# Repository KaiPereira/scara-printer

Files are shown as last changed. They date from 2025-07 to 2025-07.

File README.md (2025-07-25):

# Double Arm Scara 2D Printer

This scara printer uses a double arm scara 5-bar linkage system to be able to print in XY and utilize the floor as a bed to create a cost-effective, efficient printer/pen plotter. This printer was built for undercity, a 4 day hackathon by @lordbagel42, @vibsthebot and @KaiPereira. [Slightly Working Demo](https://www.youtube.com/shorts/rTIAOmObG48)

Pasted image 20250714064541.png

## Custom Features

- Double scara arm giving X and Y movement
- 2 wheel drivetrain which gives movement on the Z, and allows it to print in an infinitely large area
- 3D pen for the extruder/hotend giving an economical and cool way to print
- Support for Seeed XIAO RP2040 and Nema 17 motors
- Cost effective and simple design

## Cad Design

The entire design was built in Onshape by all three of us, the drivetrain is the fundamental part and uses weight to hold up the scara and 3D pen, the 3D pen is then held in using a mount and we use bearings and nema 17's for everything else. The entire project was also 3D printed aside from the electronics, screws, bearings, etc.

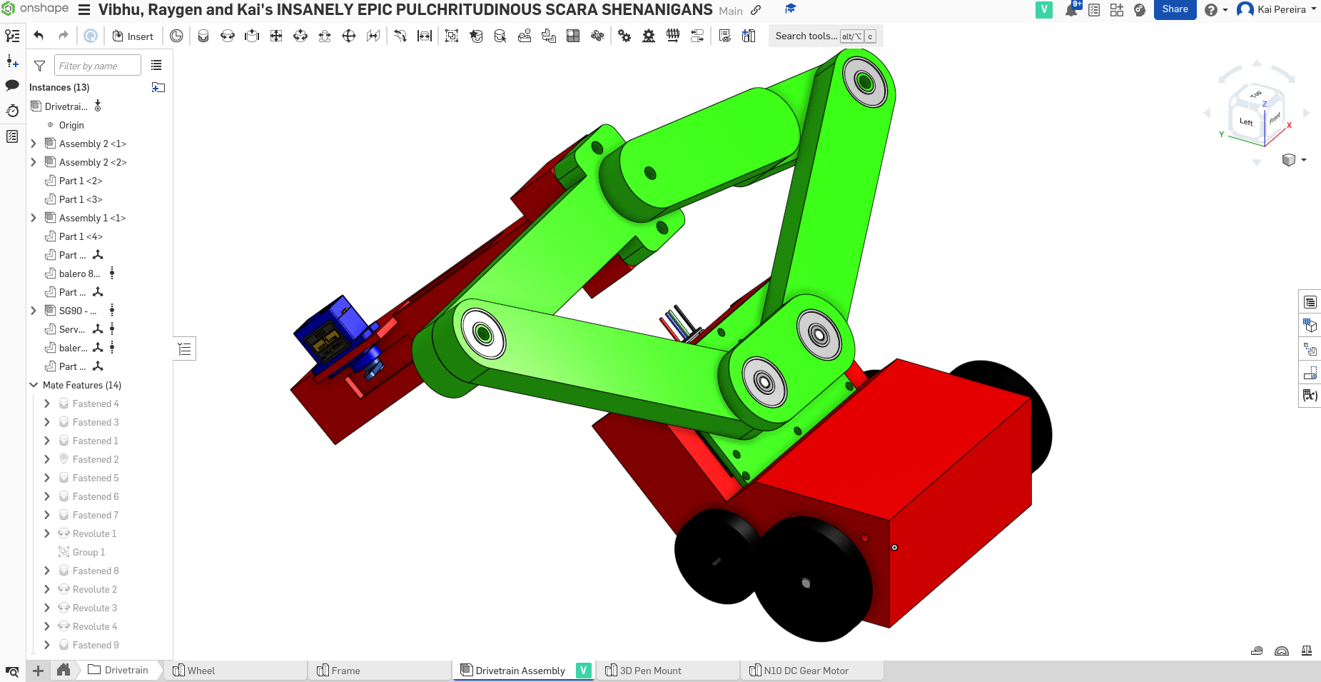
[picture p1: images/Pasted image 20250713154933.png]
Pasted image 20250713154933.png

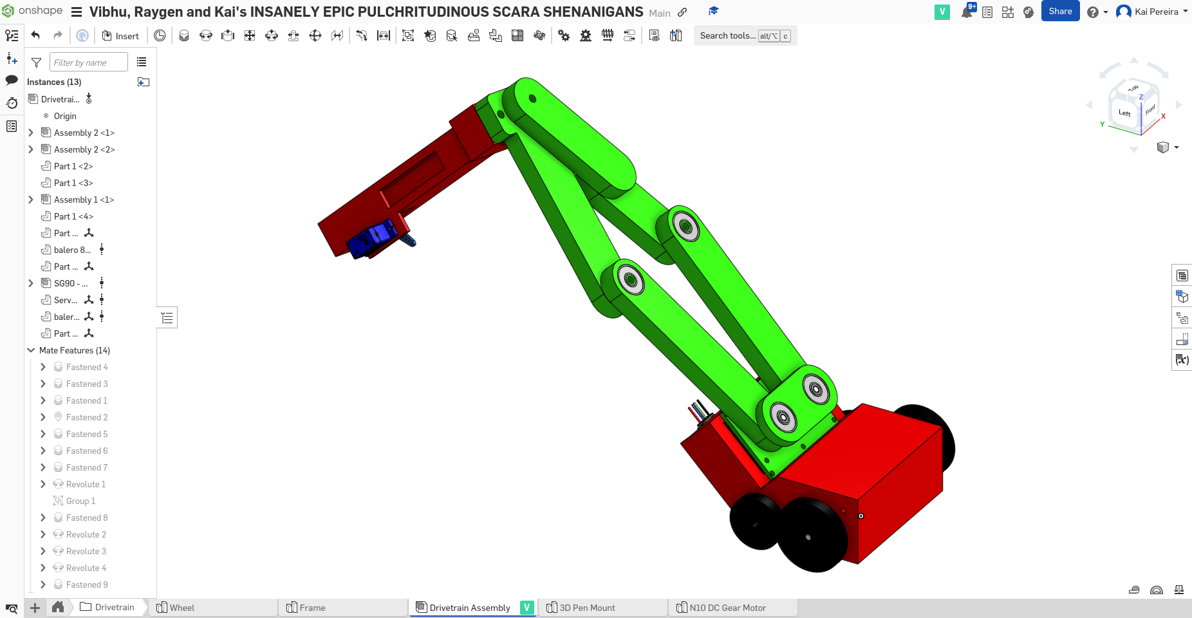
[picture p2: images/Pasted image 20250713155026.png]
Pasted image 20250713155026.png

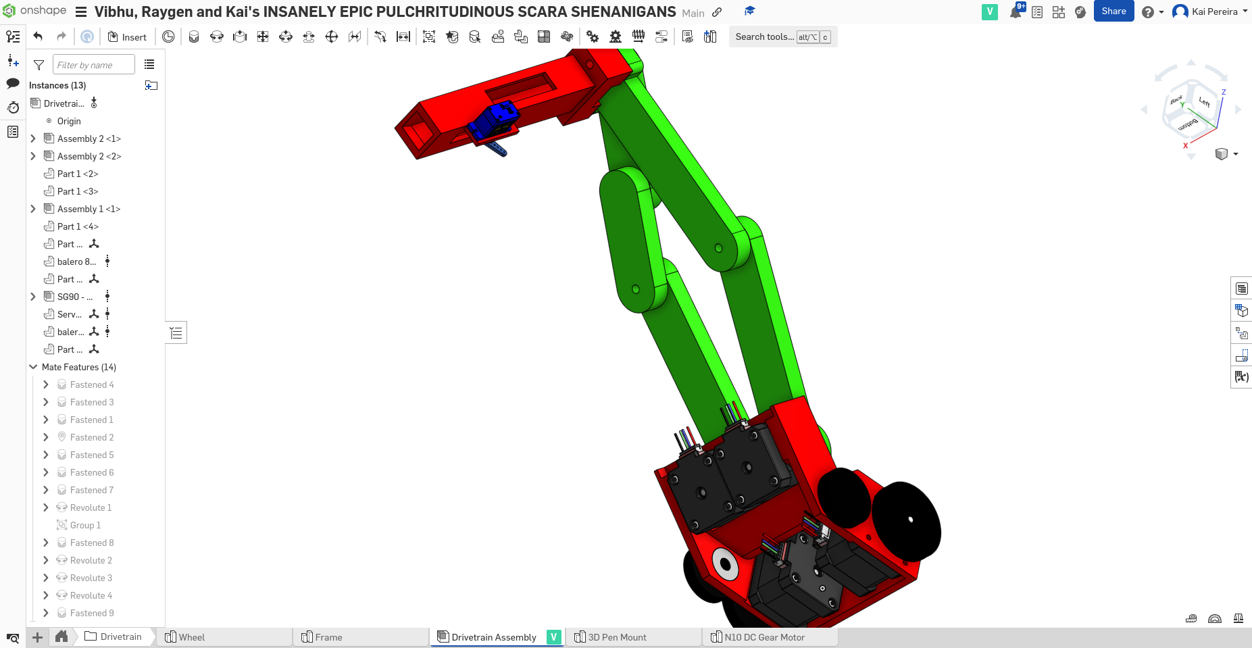
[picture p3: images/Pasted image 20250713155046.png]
Pasted image 20250713155046.png


## Electronics

The printer uses many different electronics, and we went through many, many iterations. We used NEMA 17's for our steppers, servo's for small functionality like extruding, a USB PD for power delivery, and a Seeed XIAO RP2040 for the mainboards.

Pasted image 20250714064618.png



## Firmware

The scara printer uses a **fully custom** slicer that will convert a drawing into circuit python script. We went through many different types of firmware, Marlin, grblHAL, custom, FluidNC, all of it, because we didn't have the necessary hardware to make something *normal*. And then in the end, we decided that we really just had to make something custom.

## Bill of Materials (BOM)

Here's the materials you need to build this printer:
- A LOT of PLA filament
- 4x NEMA 17 stepper motors
- 7x Ball Bearings
- 2x Seeed XIAO RP2040
- 4x Proto-PIC A4988 Stepper Motor Driver
- 2x Blot Boards
- 1x Blot USB-PD up to 20V
- 1x SG90 servo
- Lots of wires
- Assortment of screws and bolts

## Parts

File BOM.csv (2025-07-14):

4x NEMA 17 stepper motors | https://www.amazon.com/STEPPERONLINE-Stepper-63-74oz-Connector-Extruder/dp/B07LF898KN
7x 608 2RS Bearings | https://www.amazon.com/SHKI/dp/B09PKD8QZZ?gQT=22
2x Seeed Studio XIAO RP2040 | https://www.seeedstudio.com/XIAO-RP2040-v1-0-p-5026.html
4x A4988 Stepper Motor Driver | https://www.amazon.com/Stepper-Printer-StepStick-Envistia-Mall/dp/B07QT7N3T2
2x Blot Boards | https://blot.hackclub.com/
1x Blot Power Board | https://blot.hackclub.com/
1x SG90 Servo | https://www.amazon.com/Micro-Miuzei-Servos-Arduino-Airplane/dp/B0FGQ432JP
Wires
Screws and Misc

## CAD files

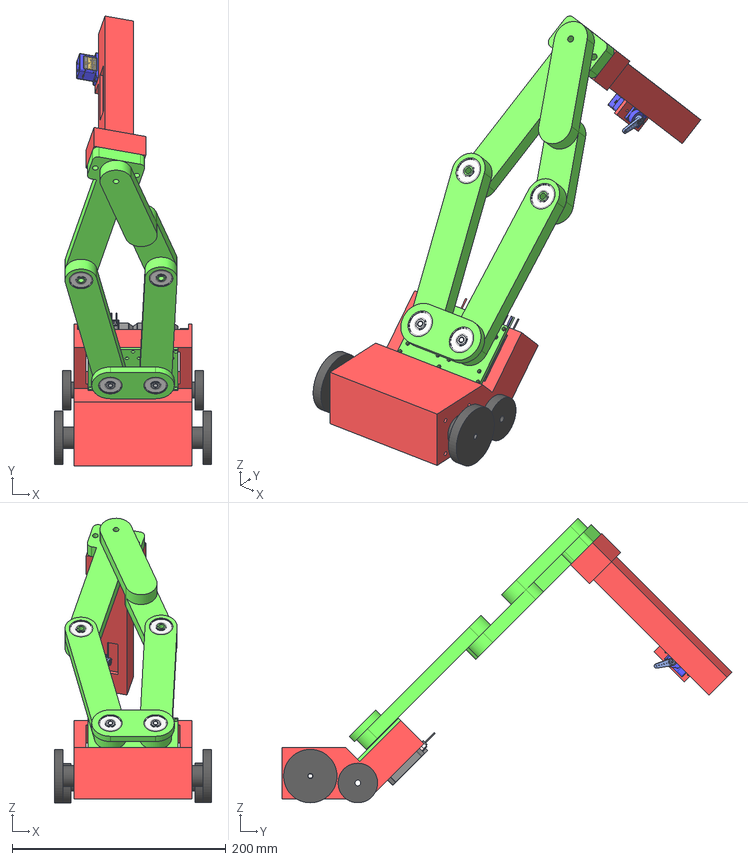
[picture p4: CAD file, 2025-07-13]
CAD/FULL ASSEMBLY.step
147.0 x 421.2 x 266.3 mm
17HE15-1504S x 4
balero 8bore 22 radio 608rs v1 x 7
Servo horn half SG90
SG90 - Micro Servo 9g - Tower Pro.1 x 13

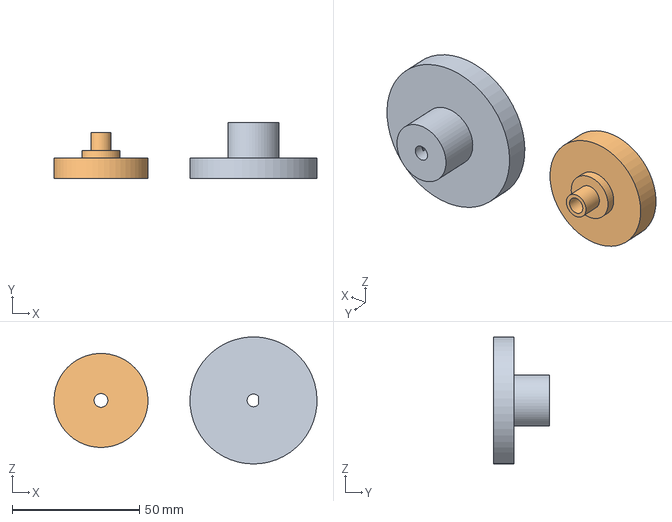
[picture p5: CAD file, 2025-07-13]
CAD/WHEELS.step
103.5 x 22.0 x 50.0 mm

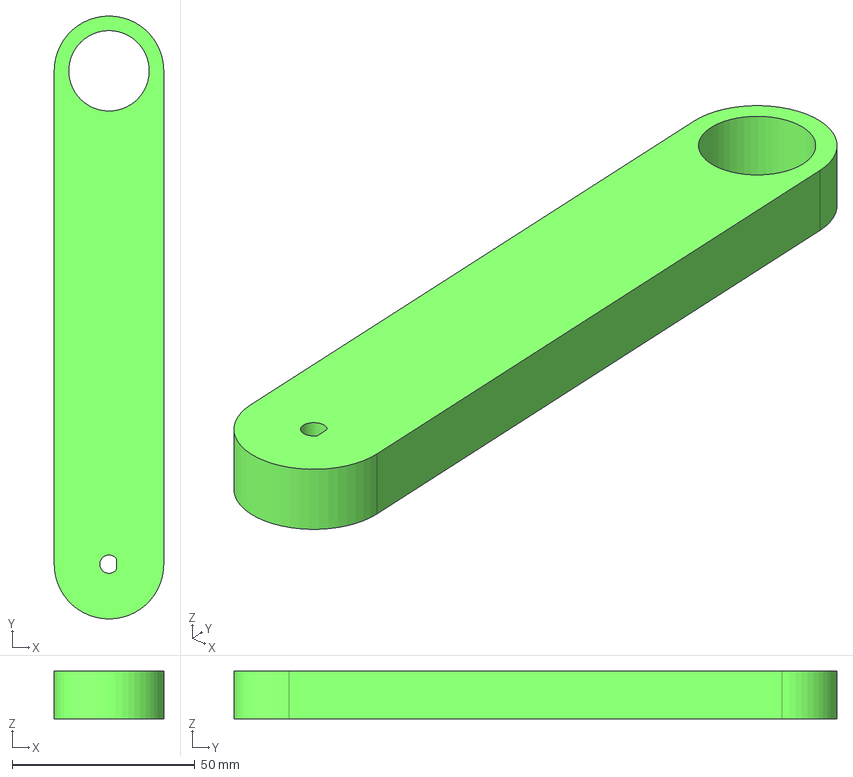
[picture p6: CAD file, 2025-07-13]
CAD/Scara Arm 1.step
30.0 x 165.0 x 13.0 mm

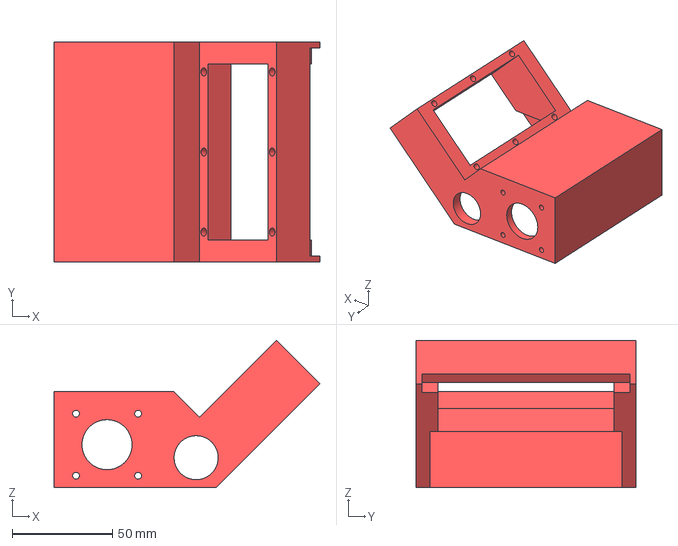
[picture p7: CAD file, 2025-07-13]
CAD/CHASSIS.step
132.9 x 110.0 x 73.7 mm

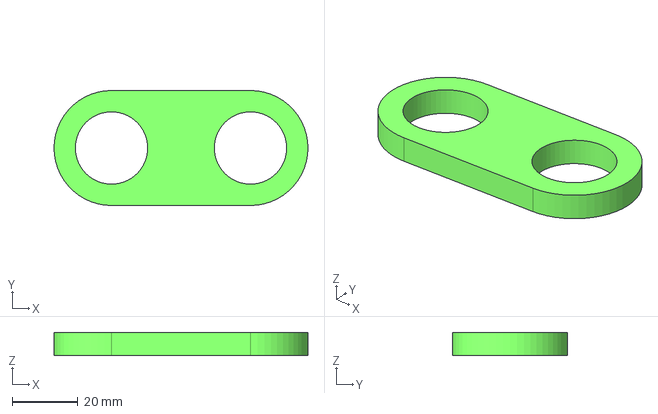
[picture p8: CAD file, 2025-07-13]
CAD/Scara Motor Holder 2.step
77.3 x 35.0 x 7.00 mm

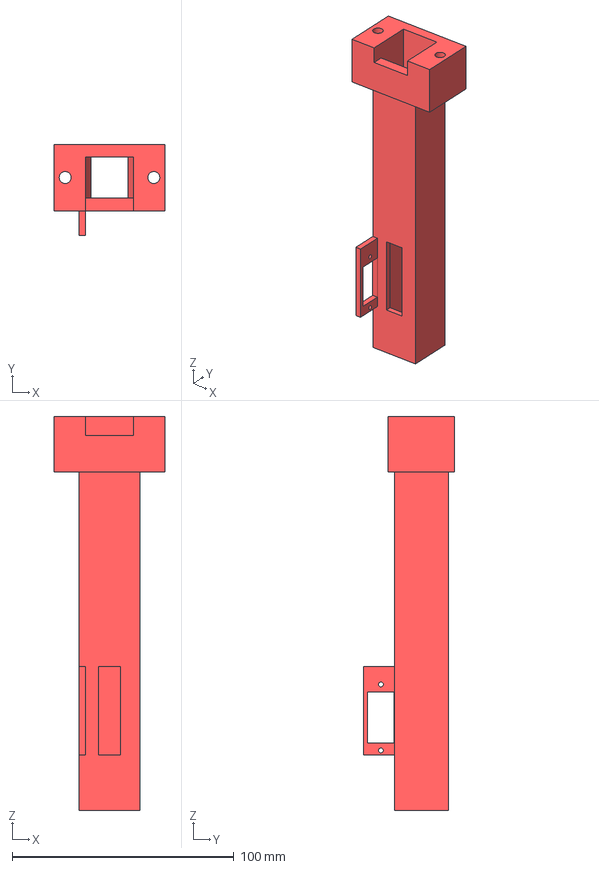
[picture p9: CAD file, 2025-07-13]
CAD/3D_PEN_MOUNT.step
50.0 x 41.2 x 177.8 mm

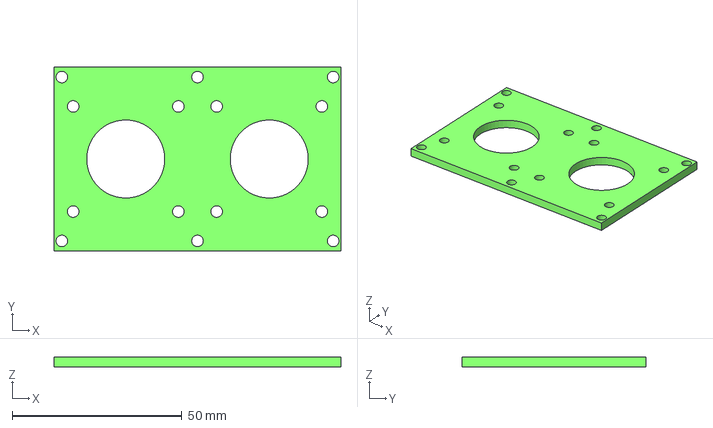
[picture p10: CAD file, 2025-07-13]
CAD/Scara Motor Holder 1.step
84.6 x 54.3 x 3.00 mm

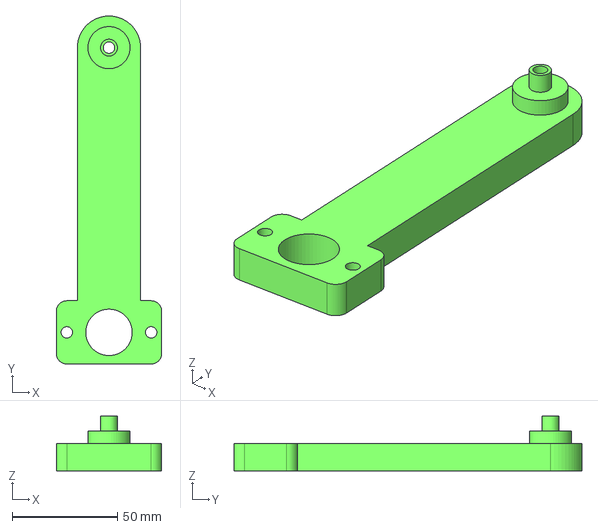
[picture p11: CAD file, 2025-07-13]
CAD/Scara Arm 2.step
50.0 x 165.0 x 26.0 mm

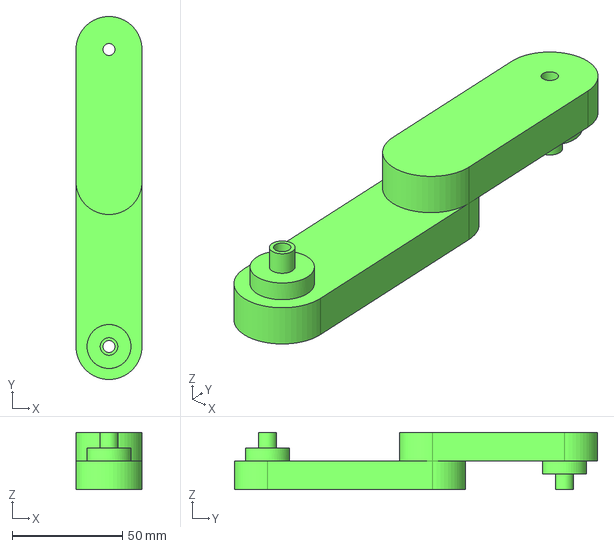
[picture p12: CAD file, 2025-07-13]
CAD/Scara Arm 3.step
30.0 x 165.0 x 26.0 mm

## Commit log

2025-07-13 added BOM
2025-07-13 added CAD files
    [3D_PEN_MOUNT.step, CHASSIS.step, FULL ASSEMBLY.step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]
2025-07-14 added bom thing
2025-07-14 updated BOM and control
2025-07-14 added bom and updated readme
    [BOM.csv]
2025-07-25 added wiring diagram
